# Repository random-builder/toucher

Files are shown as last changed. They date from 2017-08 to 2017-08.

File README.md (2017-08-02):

# Toucher

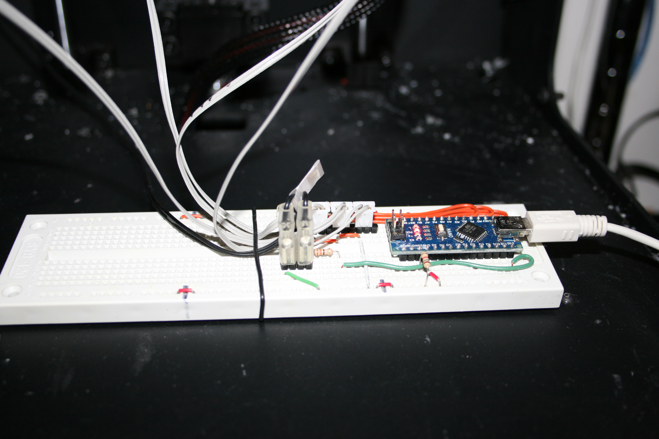
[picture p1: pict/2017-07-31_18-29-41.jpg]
board


### Purpose

Provides bed leveling FSR sensor controller for square heat beds.

### Features

- 4 sensor points
- 85C maximum bed temperature
- serial/usb terminal command interface
- flexible controller configuration and logging
- connects in place of mechanical endstop switch on Z

### Materials

Uses [Arduino Nano](https://github.com/random-builder/toucher/blob/master/docs/nano-pinout.pdf)
with [FSR-402](https://github.com/random-builder/toucher/blob/master/docs/FSR-402.pdf) sensors.
See [schema.pdf](https://github.com/random-builder/fsr-endstop/blob/master/schema/schema.pdf).

### Algorithm

Tracks fast and slow exponential averages for all channels 
to detect summary averages cross-over events.

### Reference Glass Mount

Provides "floating suspension",
when horizontal mount forces are maximal, 
vertical mount forces are minimal,
and there is a small downward force inclination.

Model: [Level: Wanhao D6 Glass Sheet Mount](https://www.thingiverse.com/thing:2461546)

### Reference Marlin Build

Works on Wanhao D6 / Monoprice Clone printer.

Github branch: [Random Builder / wanhao-d6-probe](https://github.com/random-builder/Marlin/tree/wanhao-d6-probe)

### Similar Projects

Github project: [John Socha-Leialoha FSR Endstop](https://github.com/JohnSL/FSR_Endstop)

### Setup Instructions

See [wiki page](https://github.com/random-builder/fsr-endstop/wiki).

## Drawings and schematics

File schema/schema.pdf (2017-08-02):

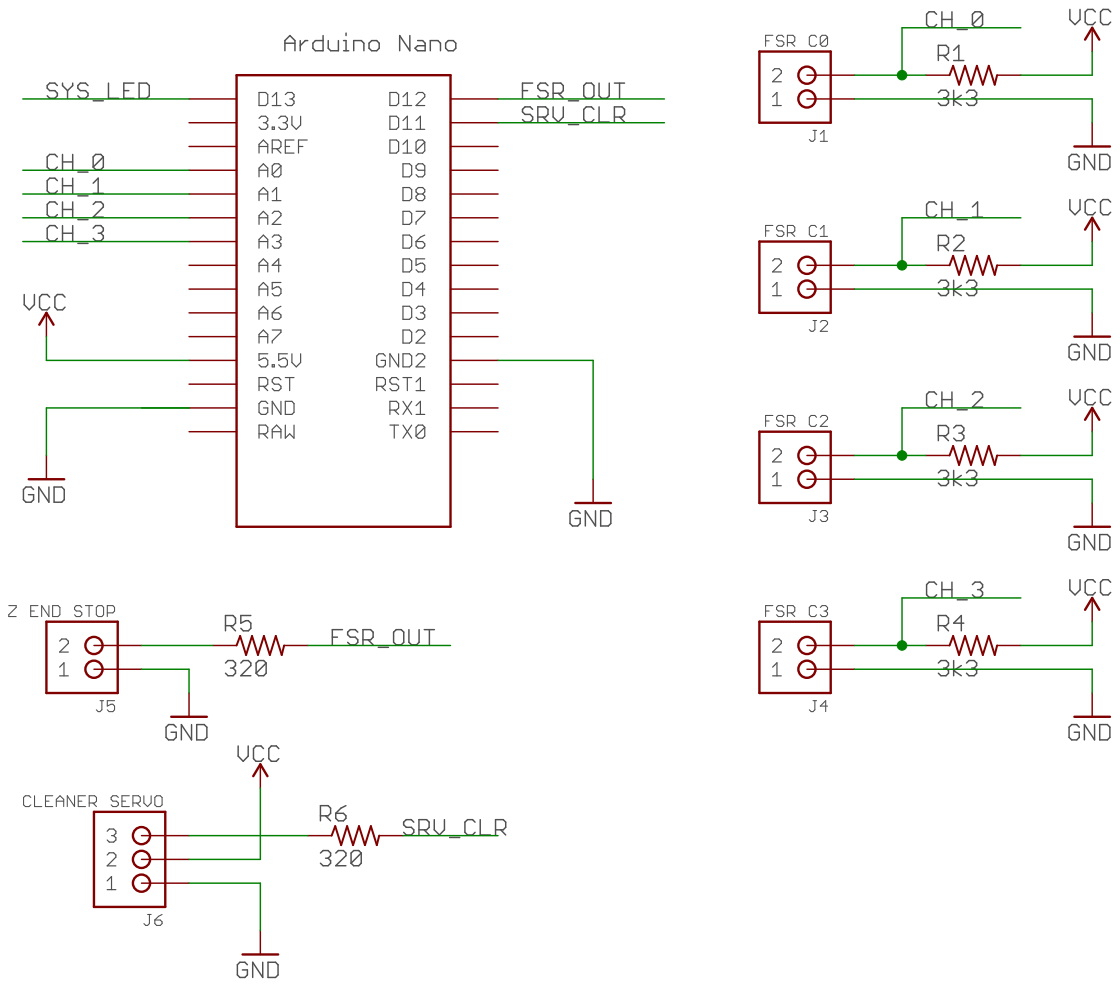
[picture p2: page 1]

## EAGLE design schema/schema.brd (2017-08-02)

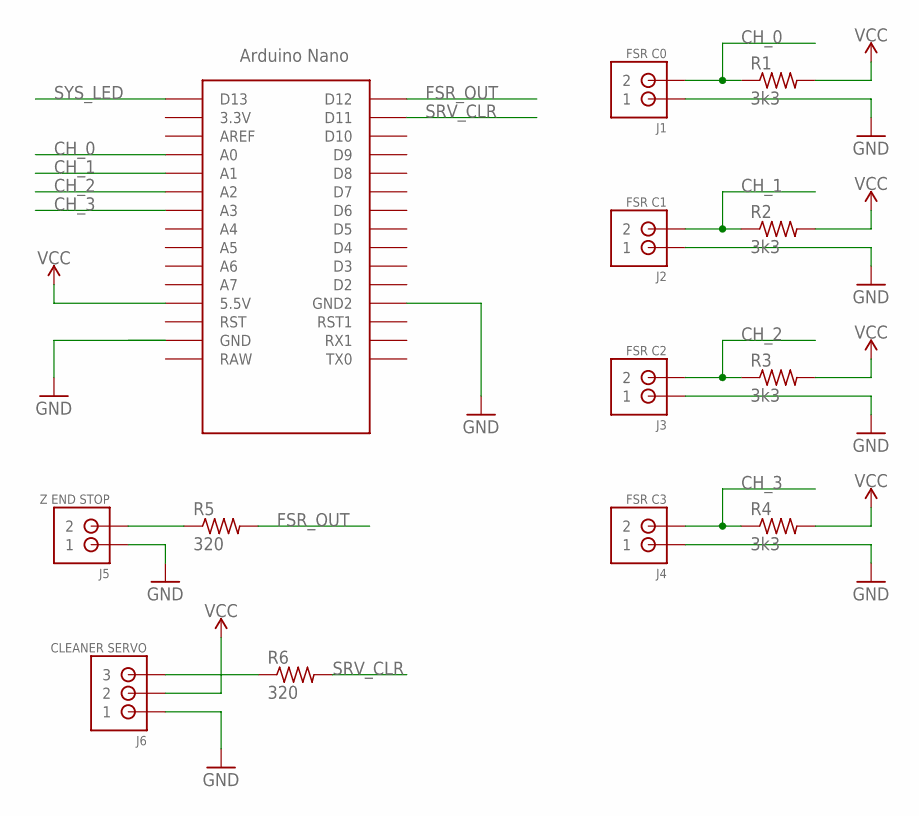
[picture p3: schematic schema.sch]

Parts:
J1: FSR C0; JST_B2B-PH_HEADER
J2: FSR C1; JST_B2B-PH_HEADER
J3: FSR C2; JST_B2B-PH_HEADER
J4: FSR C3; JST_B2B-PH_HEADER
J5: Z END STOP; JST_B2B-PH_HEADER
J6: CLEANER SERVO; JST_B3B-PH_HEADER
R1, R2, R3, R4: 3k3; 0204/5
R5, R6: 320; 0204/5
U$1: NANO

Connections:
CH_0: J1.P2 (2), R1.1, U$1.A0
CH_1: J2.P2 (2), R2.1, U$1.A1
CH_2: J3.P2 (2), R3.1, U$1.A2
CH_3: J4.P2 (2), R4.1, U$1.A3
FSR_OUT: R5.2, U$1.D12
GND: J1.P1 (1), J2.P1 (1), J3.P1 (1), J4.P1 (1), J5.P1 (1), J6.P1 (1), U$1.GND, U$1.GND1 (GND2)
unnamed: J6.P3 (3), R6.1
unnamed: J5.P2 (2), R5.1
SRV_CLR: R6.2, U$1.D11
SYS_LED: U$1.D13
VCC: J6.P2 (2), R1.2, R2.2, R3.2, R4.2, U$1.5V (5.5V)

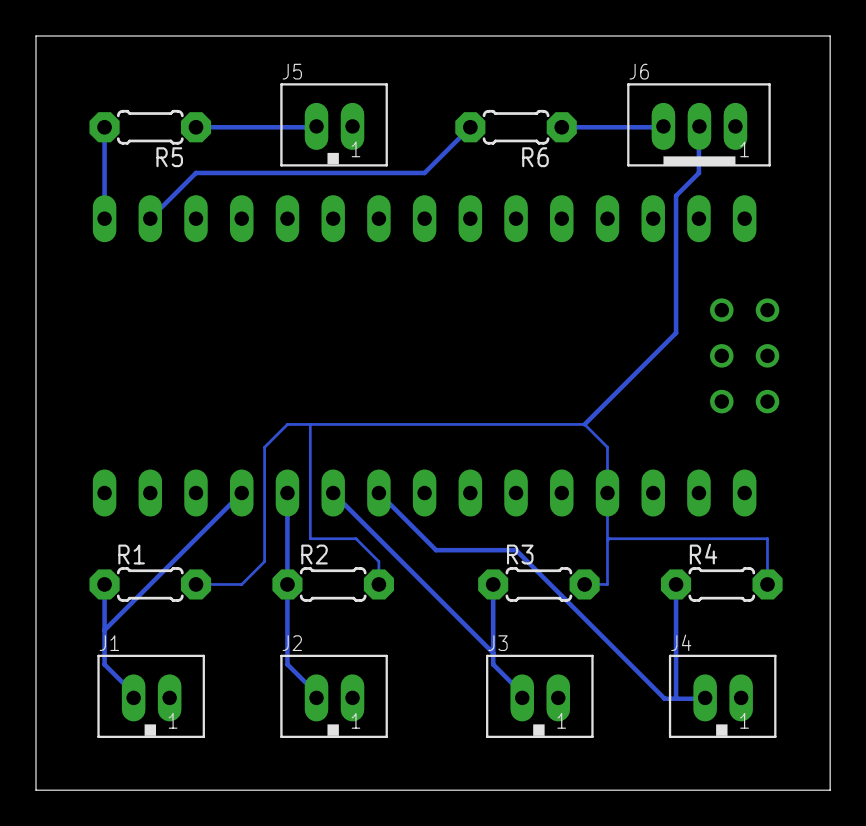
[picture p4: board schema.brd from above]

Board: 2 copper layers, 44.1 x 41.9 mm, 13 parts (0 on the bottom side), 10 nets.

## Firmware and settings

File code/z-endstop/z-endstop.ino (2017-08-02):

// main program

#include "a.h"
#include "adc.h"
#include "avg.h"
#include "cmd.h"
#include "log.h"
#include "out.h"
#include "srv.h"
#include "rom.h"

// process analog channel
void eval_avg(const byte ch) {
  cli(); // enter critical section
  boolean has = false;
  const int val = adc_result[ch];
  if ( val != ADC_NADA ) { // value pending
    has = true;
    adc_result[ch] = ADC_NADA; // value consumed
  }
  sei(); // leave critical section
  if (has) {
    avg_calc_fast(ch, val);
    avg_calc_slow(ch, val);
  }
}

// process all analog inputs
void loop_avg() {
  for (byte ch = 0; ch < AVG_CH_NUM; ch++) {
    eval_avg(ch);
  }
}

// logger params
#define LOG_PERIOD 3 // seconds
int LOG_LOOP = calc_log_loop();
int log_step = 0; // loop step

// publish periodic report
void loop_log() {
  log_step++;
  if (log_step < LOG_LOOP) {
    return;
  }
  log_step = 0;
  LOG_LOOP = calc_log_loop();
  log_fsr_stats();
}

// system params
#define SYS_LOOP 1000 // sample frequency
int sys_step = 0; // loop step
long wall_time = 0; // sample time, milliseconds
long loop_time = 220; // loop period, microseconds

// load settings
void apply_rom() {
  int rate;
  rom_read(rate, fsr_fast); avg_set_fast_rate(rate);
  rom_read(rate, fsr_slow); avg_set_slow_rate(rate);
  rom_read(out_trig_hi, fsr_hi);
  rom_read(out_trig_lo, fsr_lo);
  rom_read(out_invert, fsr_inv);
  rom_read(log_mode_mask, log_mode);
}

// measure times
void apply_time() {
  const long this_time = millis();
  loop_time = this_time - wall_time;
  wall_time = this_time;
}

// update system state
void loop_sys() {
  sys_step++;
  if (sys_step < SYS_LOOP) {
    return;
  }
  sys_step = 0;
  apply_rom();
  apply_time();
}

// auto adjust logger period to N seconds
int calc_log_loop() {
  return LOG_PERIOD * 1000000 / loop_time;
}

// report sensor status
void log_fsr_stats() {
  if (out_state) return; // log outside signal
  if (!log_has_mode(LOG_FSR_STATS_SOME)) return; // log when enabled
  char text[32];
  sprintf_P(text, PSTR("T@%-8lu | "), millis()); log_print(text);
  sprintf_P(text, PSTR("L=%-4lu | "), loop_time); log_print(text);
  for (byte ch = 0; ch < 4; ch++) {
    avg_render_chan(ch, text); log_print(text);
    avg_render_slow(ch, text); log_print(text);
    log_print_bar();
  }
  log_println();
}

// check terminal input
void loop_cmd() {
  cmd_loop();
}

// trigger output signal
void loop_out() {
  out_signal();
}

// init port
void setupComm() {
  Serial.begin(115200);
  log_println();
  log_println(F("make: " __DATE__ " " __TIME__));
}

// main setup
void setup() {
  setupComm();
  rom_setup();
  apply_rom();
  cmd_setup();
  adc_setup();
  out_setup();
  srv_setup();
}

// main loop
void loop() {
  loop_avg();
  loop_out();
  loop_sys();
  loop_log();
  loop_cmd();
}

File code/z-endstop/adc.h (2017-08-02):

// analog convertor

#ifndef ADC_H
#define ADC_H

// adc clock selector
#define ADC_PS_16    ((1 << ADPS2))
#define ADC_PS_32    ((1 << ADPS2) | (1 << ADPS0))
#define ADC_PS_64    ((1 << ADPS2) | (1 << ADPS1))
#define ADC_PS_128   ((1 << ADPS2) | (1 << ADPS0) | (1 << ADPS0)) // 100 us per conversion

// module params
#define ADC_CH_NUM 4 // channel limit
#define ADC_NADA -1 // consumed value

// use adc interrupts
void adc_setup() {
  //
  ADMUX = 0;
  ADMUX |= (1 << REFS0); // set ADC reference to AVCC
  //ADMUX |= (1 << ADLAR); // right adjust the result
  //
  ADCSRA = 0;
  ADCSRA |= (1 << ADEN); // enable adc
  ADCSRA |= (1 << ADIE); // enable  interrupt
  //ADCSRA |= (1 << ADATE); // use auto trigger
  ADCSRA |= ADC_PS_128; // prescale clock
  //
  ADCSRB = 0;
  ADCSRB |= 0; // free running mode
  //
  DIDR0 = 0; // enable all channels
  //
  sei(); // enable interrupts
  ADCSRA |= (1 << ADSC); // start conversion
}

byte adc_channel = 0; // current channel index
int adc_result[ADC_CH_NUM] = {ADC_NADA, ADC_NADA, ADC_NADA, ADC_NADA}; // adc reading for channel

// adc interrupt entry point
ISR(ADC_vect) {
  adc_result[adc_channel] = ADC; // store result
  adc_channel++; // next channel
  if (adc_channel >= ADC_CH_NUM) adc_channel = 0; // rotate index
  ADMUX = (1 << REFS0) | adc_channel; // switch channel
  ADCSRA |= (1 << ADSC); // start conversion
}

#endif // ADC_H

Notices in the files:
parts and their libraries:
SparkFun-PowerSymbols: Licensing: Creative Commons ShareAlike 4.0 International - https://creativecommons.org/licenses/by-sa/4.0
